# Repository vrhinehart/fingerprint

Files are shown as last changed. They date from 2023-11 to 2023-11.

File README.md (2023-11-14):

# Fingerprint
Arduino-based fingerprint sensor that opens an Olin College dorm door (may work on other doors too).

This repository contains the general directions, all code and electronics, and some of the mechanical parts you will need. However, you will find that you need to design your own mounts for the servo and the fingerprint sensor.

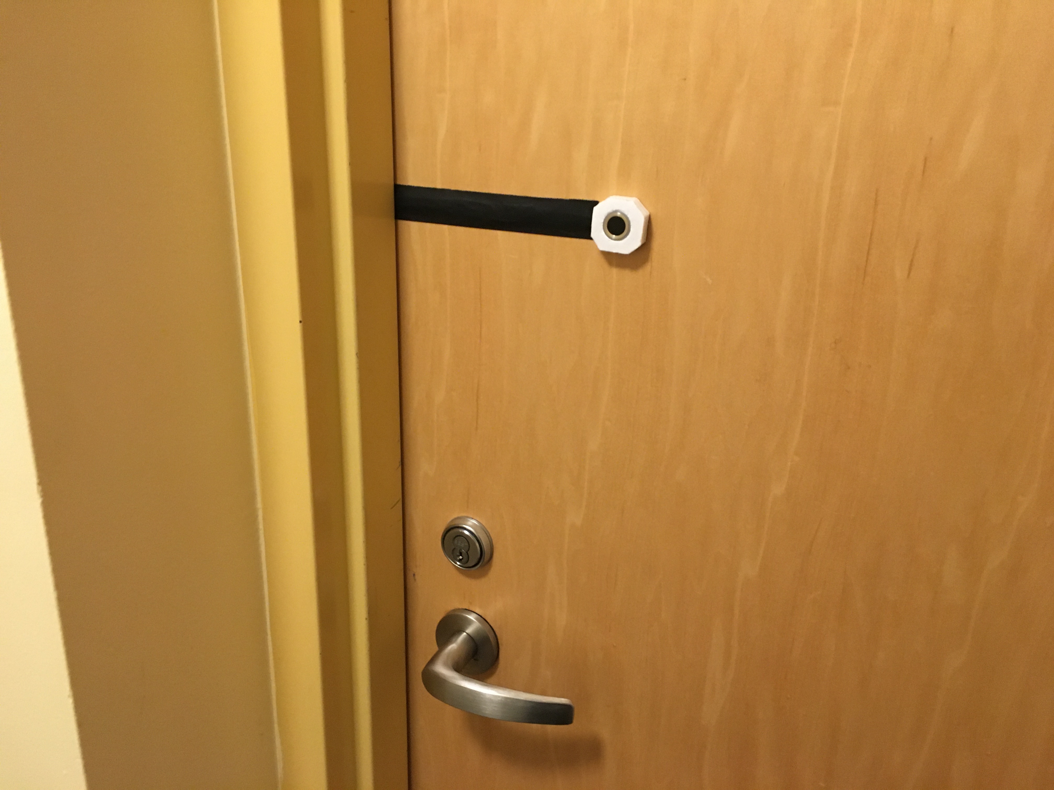
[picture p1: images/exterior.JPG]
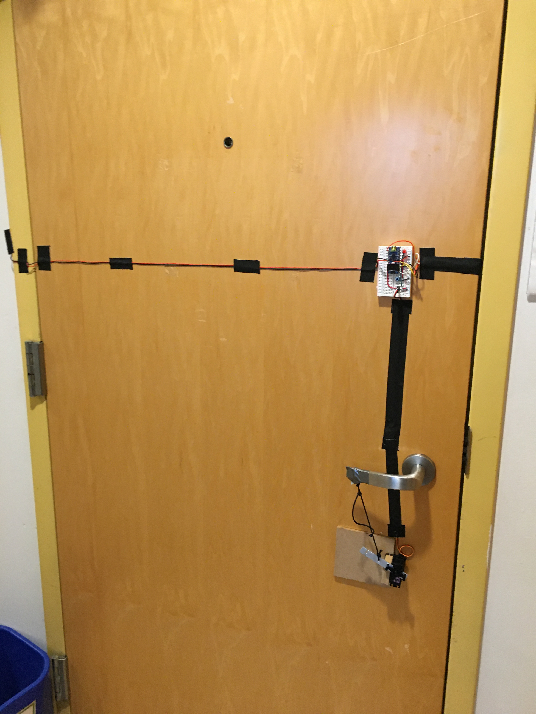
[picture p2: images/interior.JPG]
 

Parts required:
- Arduino Nano or Uno
- ID809 fingerprint sensor [DFRobot](https://www.dfrobot.com/product-2051.html) [Amazon](https://www.amazon.com/DFROBOT-Capacitive-Fingerprint-Scanner-Sensor/dp/B08JBRKB9T)
- Breadboard
- Pushbutton switch
- LED (I used red)
- High torque hobby servo (I used MG996R)
- Material for servo arm and servo mount (wood, metal, plastic)
- 5V power supply (I used cut off USB cable)
- String or Paracord
- Zip Ties
- Double sided tape (I used 3M VHB)
- Duct tape :)

Steps:
- Assemble the breadboard according to the schematic.
- 3D print, laser cut, or otherwise make the servo arm according to the included .STL or .DXF (mm) file.
- Attach the arm to the servo using the 4-arm control horn and zip ties. Wait to put in the screw.
- Mount the servo to the door as shown in the images. You can use a block of wood or whatever you want.
- Attach the fingerprint sensor and Arduino to the door as you see fit.
- Wire everything up as shown in the schematic. Use the 5V power supply for the Arduino, wired from the nearest power source as needed.
- Power the Arduino and let the servo go to its home position.
- Adjust the position of the arm so that its angle matches the pictures. Put in the servo screw.
- Install the string through the hole in the arm and duct tape the other end around the doorhandle. Tension it so that the handle is just barely at rest and there is tension on the string.

Tips:
- If the fingerprint sensor is not detected over serial, the debug LED on the Arduino will flash.
- Disconnect the Arduino from the fingerprint sensor when flashing, as the USB and sensor use the same UART.
- If the sensor LED turns cyan, it's waiting for a fingerprint. This means it was triggered to enter the verification mode, but the finger was removed. Scan a finger to exit this mode.
- You may want to cover the debug LEDs on the Arduino with tape. Otherwise they will shine in the night and possibly be confused with the "unlocked" indicator.
- The sensor supports 80 fingerprint slots, but my code only exposes 10. This can be easily changed. 
- If your finger doesn't scan reliably, try recording it to multiple slots in different positions. This ain't TouchID, it's fairly sensitive to the exact position of your finger.

Interface:
- By default, device is in fingerprint reading mode. Place your finger on the sensor to authenticate.
- When you place your finger, the servo will always move in preparation to open the door. If rejected, it will move back.
- You can put the door in "unlocked" mode by holding the button until the unlock LED illuminates. Then any fingerprint will be accepted. Turn off with another long press.
- Enter the menu by short-pressing the button (<1sec). The sensor LED will flash which slot you are on. Press the button again to change slot.
- Press the button until the LED turns blue to record a print to the selected slot. The LED will flash to confirm the slot number, then turn blue. Place your finger to record. Red indicates failure, try again.
- Press the button until the LED turns blue, then white to delete the print from the slot. The LED will breathe white to confirm deletion.

Please feel free to contact me if you want help implementing this. My code has no warranty attached, but I'd be interested to hear from you anyway.

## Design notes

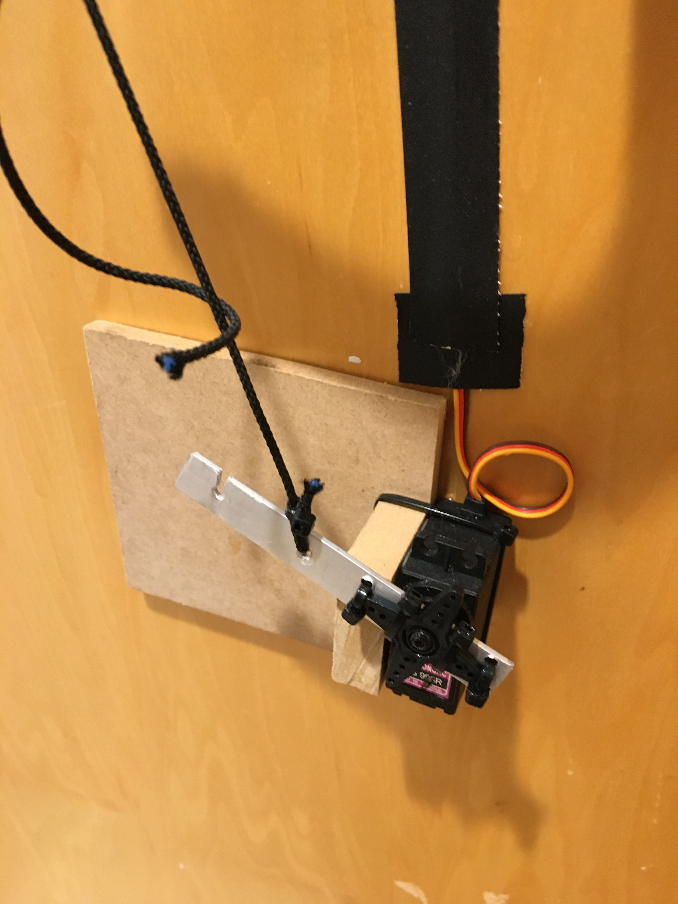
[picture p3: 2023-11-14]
images/servo.JPG

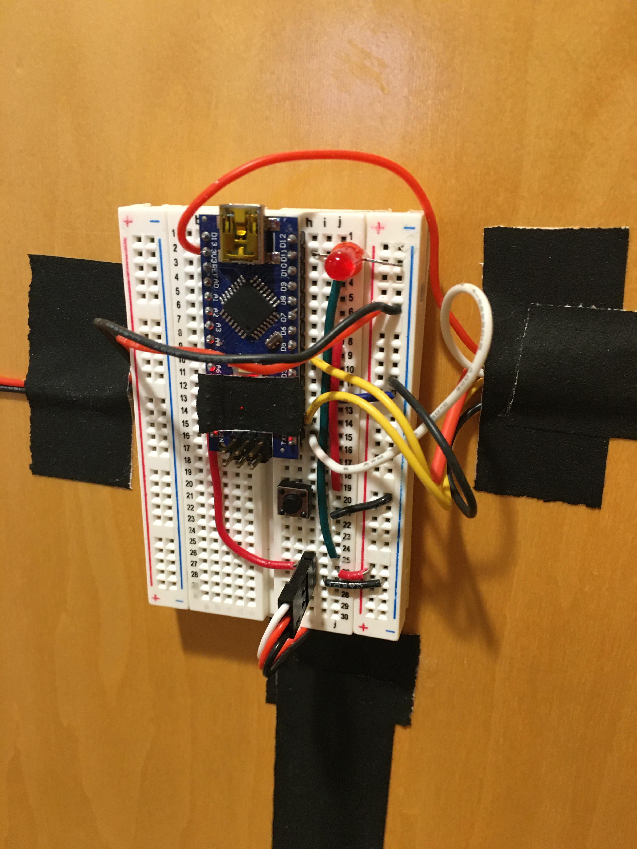
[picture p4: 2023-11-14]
images/breadboard.JPG

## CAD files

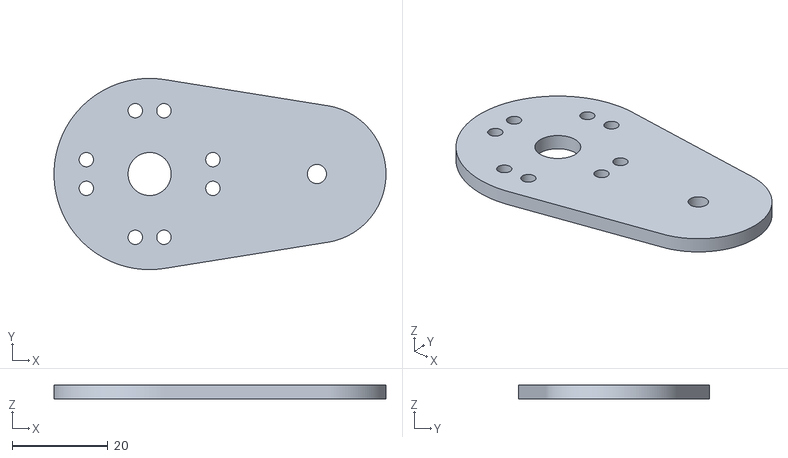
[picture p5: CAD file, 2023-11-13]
fingerprint-servo-arm.stl
69.5 x 40.0 x 3.00

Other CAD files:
fingerprint-servo-arm.dxf

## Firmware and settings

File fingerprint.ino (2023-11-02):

#include <Servo.h>

#include <DFRobot_ID809.h>

DFRobot_ID809 fingerprint;
Servo doorServo;

// Button press durations
const int dblLongDur = 2000;
const int longDur = 1000;

bool unlocked = false; // If the door is unlocked (will accept any print)
bool dbPressed = false; // Debounce state
bool pressed = false; // True state
int menuID = 0; // ID the menu is on (for writing and deleting)
unsigned long menuBlinkTime = 0; // Time of last menu ID light blink
unsigned long pressTime = 0; // Time of last (true) button press down
unsigned long dbTime = 0; // Debounce time of last state change
unsigned long servoOn = 0; //time the servo was last enabled

void dblFlash(int duration) {
  digitalWrite(13,HIGH);
  delay(duration);
  digitalWrite(13,LOW);
  delay(duration);
  digitalWrite(13,HIGH);
  delay(duration);
  digitalWrite(13,LOW);
}

void capturePrint(int ID) {
  //Fingerprint Capture
  //Set ready status
  while(true){
    //Indicate ready
    fingerprint.ctrlLED(fingerprint.eKeepsOn,fingerprint.eLEDBlue, 0);
    //Collect Fingerprint
    if((fingerprint.collectionFingerprint(/*timeout = */0)) == ERR_ID809){
      fingerprint.ctrlLED(fingerprint.eBreathing,fingerprint.eLEDRed, 0); //indicate failure
      continue; //try again
    }
    //Store Fingerprint
    if(fingerprint.storeFingerprint(ID) != ERR_ID809){
      //Indicate success
      fingerprint.ctrlLED(/*LEDMode = */fingerprint.eKeepsOn, /*LEDColor = */fingerprint.eLEDGreen, /*blinkCount = */0);
      //Wait for finger release
      while(fingerprint.detectFinger());
      //Turn off LED and return
      fingerprint.ctrlLED(/*LEDMode = */fingerprint.eNormalClose, /*LEDColor = */fingerprint.eLEDBlue, /*blinkCount = */0);
      return;
    }else{
      fingerprint.ctrlLED(fingerprint.eKeepsOn,fingerprint.eLEDRed, 0);
      delay(1000);
      //delay(10000);
      //Serial.println(fingerprint.getErrorDescription());
    }
    //Wait for finger release
    while(fingerprint.detectFinger());
  }
}

int verifyPrint(){
  //Collect Fingerprint
  while(!fingerprint.detectFinger()){
    //Show ready if waiting for finger.
    fingerprint.ctrlLED(fingerprint.eKeepsOn,fingerprint.eLEDCyan, 0);
    delay(200);
  }
  if(fingerprint.collectionFingerprint(/*timeout = */0) == ERR_ID809){
    fingerprint.ctrlLED(fingerprint.eBreathing,fingerprint.eLEDRed, 1); // show error
    delay(1000);
  }
  // Search fingerprint
  int readID = fingerprint.search();
  if(readID != 0) {
    //indicate success
    fingerprint.ctrlLED(fingerprint.eFastBlink,fingerprint.eLEDGreen,readID);
  } else {
    //Indicate rejection
    dblFlash(50);
    fingerprint.ctrlLED(fingerprint.eFastBlink,fingerprint.eLEDRed,2);
  }
  return readID;
}

void openDoor(){
  doorServo.attach(10);
  servoOn = millis();
  doorServo.write(130);
}

void setup() {
  //setup debug LED
  pinMode(13,OUTPUT); // debug LED
  doorServo.attach(10); // motor
  servoOn=millis();
  pinMode(5,INPUT_PULLUP); // button
  pinMode(11,OUTPUT); // door unlocked LED
  pinMode(4,INPUT); // finger sensor ring
  digitalWrite(13,LOW);
  //Setup sensor
  Serial.begin(115200);
  fingerprint.begin(Serial);
  delay(500); //wait for connection
  while(fingerprint.isConnected() == false){
    //connection failed - flash error
    dblFlash(500);
    delay(1000);
  }
  fingerprint.setSecurityLevel(1);
  doorServo.write(0);
}

void loop() {
  // Servo detachment
  if(millis()-servoOn > 2000 && doorServo.attached()){
    doorServo.write(0);
    delay(2000);
    doorServo.detach();
  }
  // Menu blinking and timeout
  if(menuID != 0){ // we're in the menu mode
    if((millis() - menuBlinkTime) > (500*menuID + 1000)){
      //It has been 1 second past the end of the last blink
      menuBlinkTime = millis();
      fingerprint.ctrlLED(fingerprint.eFastBlink,fingerprint.eLEDMagenta,menuID);
    }
    if((millis() - pressTime) > 15000){
      menuID = 0; // exit menu
    }
  }
  // Finger scanning
  if(digitalRead(4)){
    if(unlocked){
      // If unlocked, just open the door and flash green.
      openDoor();
      fingerprint.ctrlLED(fingerprint.eFastBlink,fingerprint.eLEDGreen,1);
    } else {
      // If locked, scan print and open door if accepted.
      //Prepare servo while fingerprint is scanning.
      doorServo.attach(10);
      doorServo.write(70);
      if(verifyPrint() != 0){
        openDoor();
        //Wait for finger release
        while(fingerprint.detectFinger());
      }
    }
  }
  // Debounce
  int button = !digitalRead(5);
  if(dbPressed != button){
    dbPressed = button;
    dbTime = millis();
  }
  // True button press handling
  if(millis() - dbTime > 40){ // Button has been pressed longer than 70ms
    if(dbPressed != pressed){ // New button state is different from previous true state
      pressed = dbPressed; // Update true state
      if(pressed){
        pressTime = millis(); // Update pressTime if the button is down
      } else {
        if((millis()-pressTime) > dblLongDur){ // if double long press
          if(menuID){ // If in the menu
            // one white breath to indicate delete
            fingerprint.ctrlLED(fingerprint.eBreathing,fingerprint.eLEDWhite, 1);
            fingerprint.delFingerprint(menuID); // delete print
            menuID = 0; //exit menu
          }
        } else if((millis()-pressTime) > longDur){ // if long press
          if(menuID){ //if in the menu
            // Flash ID in blue
            fingerprint.ctrlLED(fingerprint.eFastBlink,fingerprint.eLEDBlue,menuID);
            delay(500*menuID + 200); // wait for blinking to be done
            capturePrint(menuID);
            menuID = 0; 
          } else {
            unlocked = !unlocked; // long press outside menu locks/unlocks.
          }
        } else {
          dblFlash(100);
          menuID++; // Increment menu ID
          if(menuID > 10){
            menuID = 1;
          }
          menuBlinkTime = 0; //reset blink time to blink new ID
        }
      }
    } else { // New button state is the same as previous button state
      if(pressed){
        if((millis()-pressTime) > dblLongDur){ // if double long press
          if(menuID){ // if in the menu
            // Set LED constant white to indicate erase.
            fingerprint.ctrlLED(fingerprint.eKeepsOn, fingerprint.eLEDWhite, 0);
          }
        } else if((millis()-pressTime) > longDur){ // if long press
          if(menuID){ //if in the menu
            // Set LED constant blue to indicate write.
            fingerprint.ctrlLED(fingerprint.eKeepsOn, fingerprint.eLEDBlue, 0);
          } else { // not in the menu
            if(unlocked){
              analogWrite(11,0); // turn off unlocked warning
            } else {
              analogWrite(11,50); // light unlocked warning
            }
          }
        }
      }
    }
  }
}

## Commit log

2023-11-02 Added schematic
    [electronics.kicad_pcb, electronics.kicad_sch]
2023-11-02 Added fingerprint arm STL
    [fingerprint-servo-arm.stl]
2023-11-02 Add Arduino code
2023-11-03 Added servo
    [electronics.kicad_sch]
2023-11-13 Updated servo arm
2023-11-13 Updated servo arm, added DXF
    [fingerprint-servo-arm.dxf, fingerprint-servo-arm.stl]
